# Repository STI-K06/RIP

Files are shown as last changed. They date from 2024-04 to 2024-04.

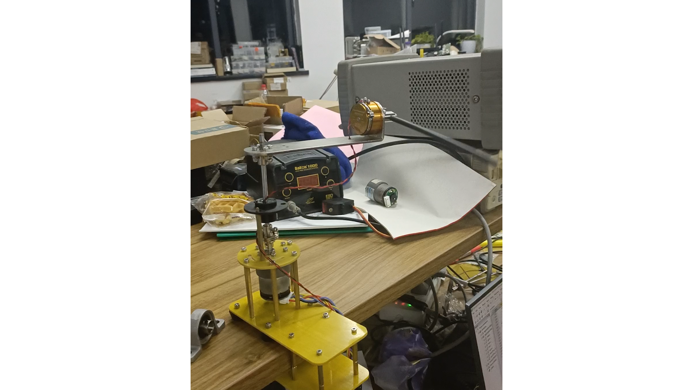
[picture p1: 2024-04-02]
hw/picture/倒立摆.png

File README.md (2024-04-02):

# 旋转倒立摆
RIP refer to *rotating inverted pendulum*  
这个分支是旋转倒立摆整体分支，分以下部分  
## doc
**存放一些文档，如题目和报告**
* 这里存放了题目和我们组当时的报告
## hw
**存放硬件与机械部分以及倒立摆实物图**  
* 硬件部分stl文件为对倒立摆所需各个部件的建模
* 根据建模并得出dxf文件用于雕刻，采用雕刻环氧板的方式搭建机械
* 此次是采用洞洞板直接焊接，因此没有设计PCB
## sw
**存放主控代码以及视觉部分python代码**  
* 主控部分采用stm32cubemx进行配置，用keil软件进行main函数编程
* 此次主控采用的是stm32f103c8t6
## 原理介绍(以后补)

## 视频链接
视频参见**https://www.bilibili.com/video/BV1mm4y1n7Gn**

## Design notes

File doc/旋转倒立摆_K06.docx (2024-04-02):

旋转倒立摆

摘要：本系统实现了一个旋转倒立摆。该系统利用STM32F103C8T6单片机作为主控制器，与电机驱动模块、减速直流电机、旋转臂、摆杆和角位移传感器一起构成摆杆角度和电机速度的双闭环调速系统。控制方式采用串级PID控制，选择减速直流电机带动旋转臂旋转，利用编码器测量电机转动的脉冲数和速度，实现速度环控制。采用角位移传感器测量摆杆的偏角，实现角度环控制。最终，系统能够较好的实现起摆、倒立、360度倒立旋转等功能，同时具有较强的抗扰动性能。

关键词：角度测量；电机控制；倒立平衡

# 1、 系统方案

## 1. 比较与选择

### 1.1 角度测量方案

方案一：三轴陀螺仪

方案二：电位器

方案比较与选择：方案一选用三轴陀螺仪检测摆杆的偏转角度，优点是可以较为精确的计算摆杆的偏转角度，缺点是传感器必须要固定在摆杆上，同时需与MCU直连以进行通信，给硬件的搭建与连接及软件的编写大大增加了难度，可行性较差。方案二选用电位器测量摆杆的偏转角度，优点是其可作为摆杆的转动主轴，可有效降低硬件部分的复杂性，并增强稳定性，且其较为简单的原理也便于软件的编写。缺点是测量时可能会因电位器的固有误差导致角度换算误差。在本设计中，摆杆的结构设计方面要求较高，不适于将传感器固定在摆杆上，且使用较高精度的电位器时同样能达到接近陀螺仪的测量效果。因此，选择方案二来实现摆杆角度的测量。

### 1.2 摆杆驱动方案

方案一：步进电机

方案二：直流减速电机

方案比较与选择：方案一采用步进电机驱动旋转臂，具有动态响应快、易于启停、易于正反转的切换及变速的优点。缺点是它以步进式跟进，角度小于一个步进角时是系统的响应盲区。方案二采用直流减速电机驱动旋转臂，优点是驱动电路简单，扭矩大，稳定性强，负载能力强。缺点是相较于直流电机转速较低。在本设计中，对电机的转速要求较小，对角度的响应精细程度和稳定性要求较大，故直流减速电机方案更为合适，因此选择方案二。

### 1.3 摆杆材料及结构选择

方案一：直径5mm长度18cm的不锈钢柱做摆杆

方案二：直径5mm长度18cm的中空碳纤维管做摆杆，尾端增加重物

方案比较与选择：方案一使用不锈钢柱作为摆杆，优点是材料易得、结构简单。缺点是转动惯量与重力力矩比值更小，由重力引起的角加速度更快，摆动更快，不利于稳定；并且整体质量更大，电机运动的阻力更大。方案二使用碳纤维管做摆杆，优点是摆杆质量可以忽略，整体转动惯量与重力力矩比值更大，由重力引起的角加速度更小，更容易控制；并且整体质量更小，电机运动的阻力更小，利于控制。缺点是材料不易得，重物的选择需要考虑。在本设计中，为使倒立摆更容易控制和达到稳态，故采用方案二。

### 1.4 固定倒立摆的底座结构选择

方案一：将倒立摆置于一个平面上，用重物压住平面

方案二：将倒立摆通过上下两面夹持的方式固定在桌子上，并用橡胶垫增大摩擦力和稳定性

方案比较与选择：方案一将倒立摆置于一个平面上，用重物压住平面，优点是结构简单，制作快。缺点是符合要求的重物质量较大，实际上不好操作。方案二将倒立摆夹持在桌子上，优点是只要桌子足够稳定，倒立摆基本上不会剧烈晃动。缺点是设计较为复杂。在本设计中，为了得到更好的稳定效果，故采用方案二。

## 2. 方案描述

系统框图如图1所示。在接收到任务执行指令后，STM32主控通过ADC通道采集角位移传感器反馈值换算成角度，并利用编码器计算得电机转动的脉冲数和转动速度。主控根据反馈值进行双环PID计算，输出PWM控制直流电机带动旋转臂运动。综上，摆杆在直流减速电机的控制之下顺利倒立，完成题目要求的相关任务。

图1 系统框图

# 2、 理论分析与计算

## 1. PID算法

如图2所示，当电位器反馈摆杆发生位移时，其变化的模拟量被MCU的AD所采集，MCU运用PID算法计算输出PWM，以控制电机的转向及转速，进而对摆杆的实时位置进行微控。

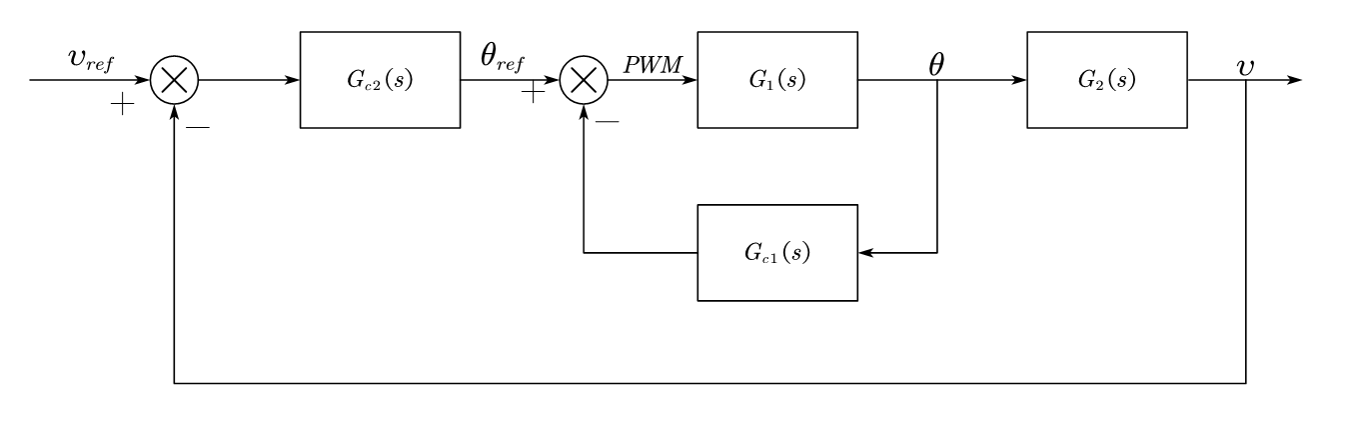
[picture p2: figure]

图 2 PID算法理论模型

## 2. 机械机构

旋转倒立摆结构如图3所示。倒立摆底座为上下两片环氧板，通过夹持方式夹在桌角。电机与底座通过6根M3铜柱相连，固定在底座上。电机转轴通过两个法兰联轴器与5mm不锈钢柱相连。不锈钢柱通过过孔导线环与转杆相连。转杆尾端放置角位移传感器。角位移传感器连接着摆杆，摆杆末端用法兰与铜柱构成重物。

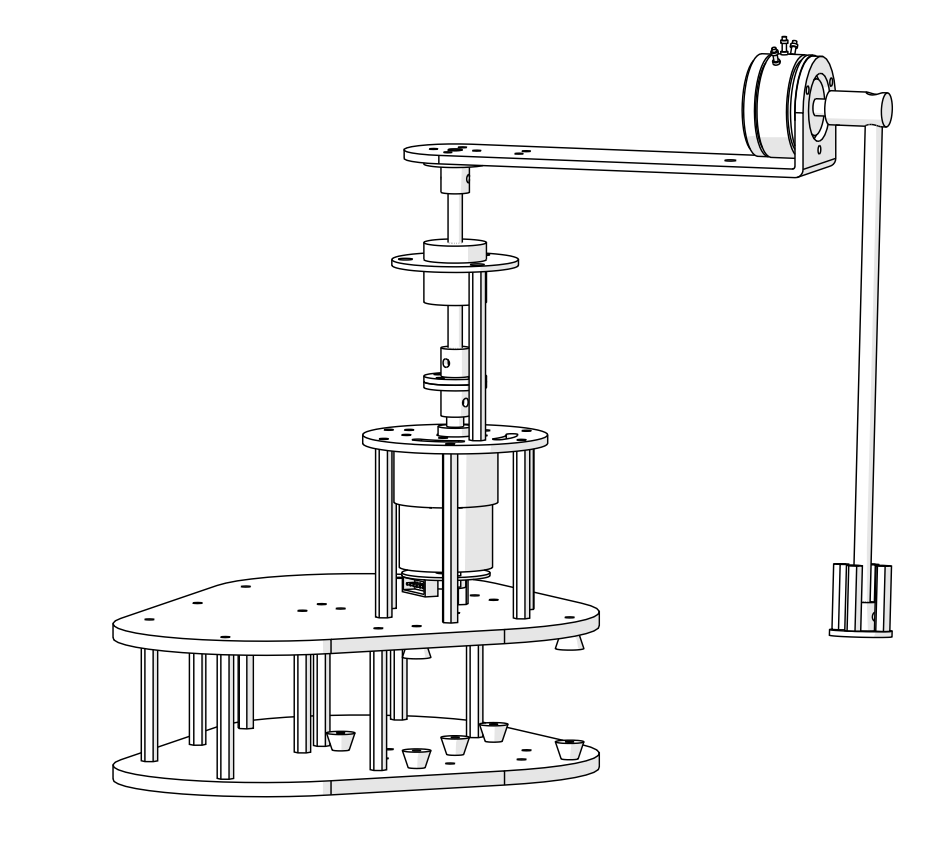
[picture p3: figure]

图3旋转倒立摆机械结构

# 3、 电路与程序设计

## 1. 电机驱动电路

如图4所示，直流电机驱动的主体为DRV8872直流电机驱动芯片，通过输入两通道PWM波的方式来控制直流电机的转速和转动方向。主控STM32可以通过输出特定1KHz频率、不同占空比的PWM波来对直流电机的转速和转动方向。

图4 电机驱动电路

## 2. 软件程序设计

程序设计流程图如图5所示。本设计中使用主控STM32控制系统，接收角度传感器数据，并利用编码器测量速度，通过PID计算输出PWM控制电机运动，完成任务要求的一系列动作。

图 5 程序设计流程图

# 4、 测试方案与测试结果

## 1. 测试环境

类型 | 品牌 | 型号
其他 | 卡西欧、SYNTEK | HS-70W型秒表、SYJDC200型角度尺

## 3. 测试方案

### 2.1摆杆起摆测试

### 摆杆从处于自然下垂状态开始，驱动电机带动旋转臂旋转使摆杆摆动，使摆角达到或超过-60°~ +60°。

### 2.2摆杆完成圆周运动测试

### 从摆杆处于自然下垂状态开始，增大摆杆的摆动幅度，直至完成圆周运动。

### 2.3摆杆由外力拉起保持倒立测试

### 外力拉起摆杆至接近 165°位置，外力撤除同时，启动控制旋转臂使摆杆保持倒立状态。

### 2.4摆杆自动起摆保持倒立测试

### 从摆杆处于自然下垂状态开始，控制旋转臂作往复旋转运动，使摆杆倒立。

### 2.5 摆杆受干扰测试

### 在摆杆保持倒立状态下，施加干扰后摆杆能继续保持倒立或 2s 内恢复倒立状态。

### 2.6 摆杆保持倒立而旋臂做圆周运动测试

### 在摆杆保持倒立状态的前提下，旋转臂作圆周运动超过一圈。

## 4. 测试结果与数据

### 3.1 摆杆起摆测试数据如表1所示

表1摆杆起摆测试

| 测试结果
序号 | 是否成功 | 起摆时间
1 | 成功 | 2.1s
2 | 成功 | 2.4s
3 | 成功 | 2.3s

### 3.2 摆杆完成圆周运动测试数据如表2所示

表2摆杆完成圆周运动测试

| 测试结果
序号 | 是否成功 | 使用时间
1 | 成功 | 3.1s
2 | 成功 | 3.5s
3 | 成功 | 3.7s

### 3.3 摆杆由外力拉起保持倒立测试数据如表3所示

表3摆杆由外力拉起保持倒立测试

| 测试结果
序号 | 是否成功 | 转动角度
1 | 成功 | 10°
2 | 成功 | 20°
3 | 成功 | 18°

3.4 摆杆自动起摆保持倒立测试数据为表4所示

表4 摆杆自动起摆保持倒立测试

| 测试结果
序号 | 是否成功 | 使用时间
1 | 成功 | 5.1s
2 | 成功 | 5.5s
3 | 成功 | 5.7s

3.5 摆杆受干扰测试数据为表5所示

表5 摆杆受干扰测试

| 测试结果
序号 | 是否成功
1 | 成功
2 | 成功
3 | 成功

3.6 摆杆保持倒立而旋臂做圆周运动测试数据为表6所示

表6 摆杆保持倒立而旋臂做圆周运动测试

| 测试结果
序号 | 是否成功 | 使用时间
1 | 成功 | 4.2s
2 | 成功 | 4.4s
3 | 成功 | 4.7s

## 5. 测试结果分析

### 4.1摆杆起摆测试

### 由测试结果知，摆杆可以迅速起摆到-60°~ +60°，满足题目要求。

### 4.2摆杆完成圆周运动测试

### 由测试结果知，摆杆可以迅速起摆直至完成圆周运动，满足题目要求。

### 4.3摆杆由外力拉起保持倒立测试

### 由测试结果知，摆杆由外力拉起后能够迅速保持倒立，满足题目要求。

### 4.4摆杆自动起摆保持倒立测试

### 由测试结果知，摆杆可以自动起摆并迅速保持倒立，满足题目要求。

### 4.5 摆杆受干扰测试

### 由测试结果知，摆杆受干扰后仍能保持倒立状态，满足题目要求。

### 4.6 摆杆保持倒立而旋臂做圆周运动测试

### 由测试结果知，摆杆在保持倒立状态的同时能够使旋臂做圆周运动，满足题目要求。

### 综上所述，本系统能够完成题目的基本要求和发挥要求。

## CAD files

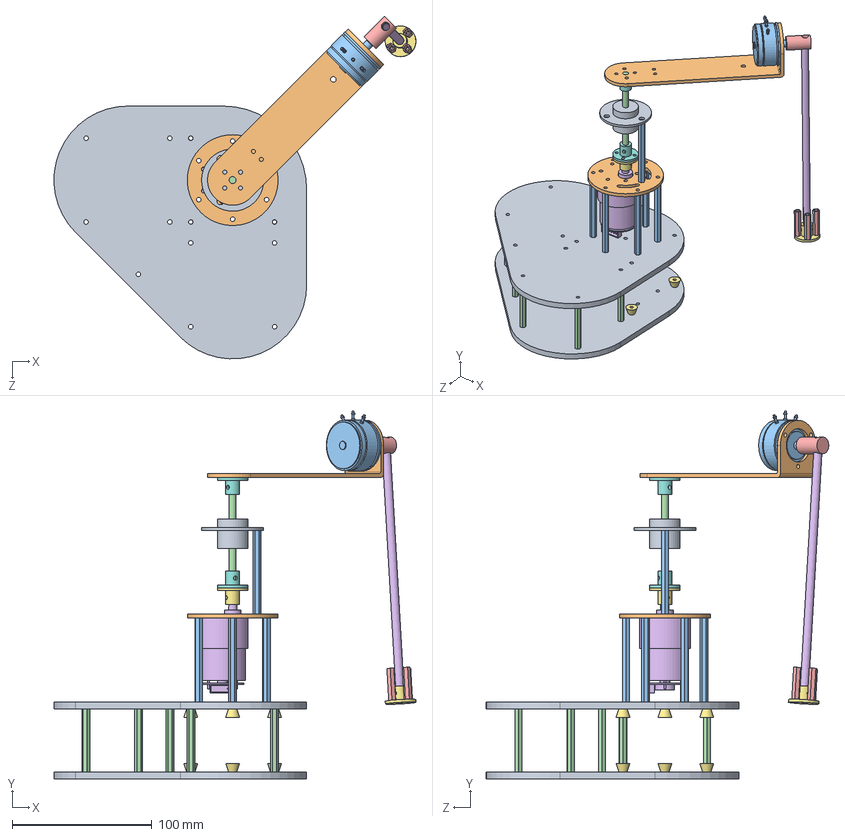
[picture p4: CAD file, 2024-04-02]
hw/stl/旋转倒立摆.SLDASM
259.3 x 263.3 x 245.4 mm
倒立摆底座 x 2
中间连接板
M3铜柱50mm x 7
M3铜柱45mm x 9
M3铜柱23mm x 4
直流减速电机带编码器
法兰联轴器 - 6mm x 2
法兰联轴器 x 2
过孔导线环
角位移传感器支架
角位移传感器
不锈钢柱子
L型联轴器
中通碳管
橡胶垫 x 10

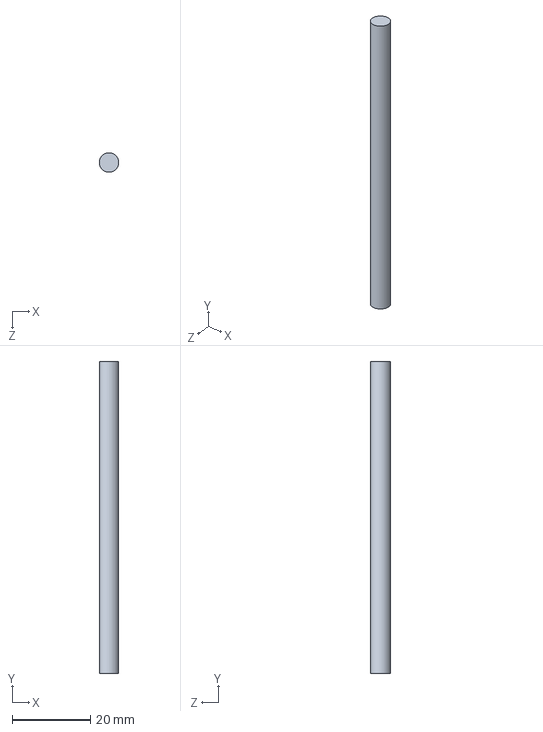
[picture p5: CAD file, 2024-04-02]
hw/stl/不锈钢柱子.SLDPRT
5.00 x 80.0 x 5.00 mm

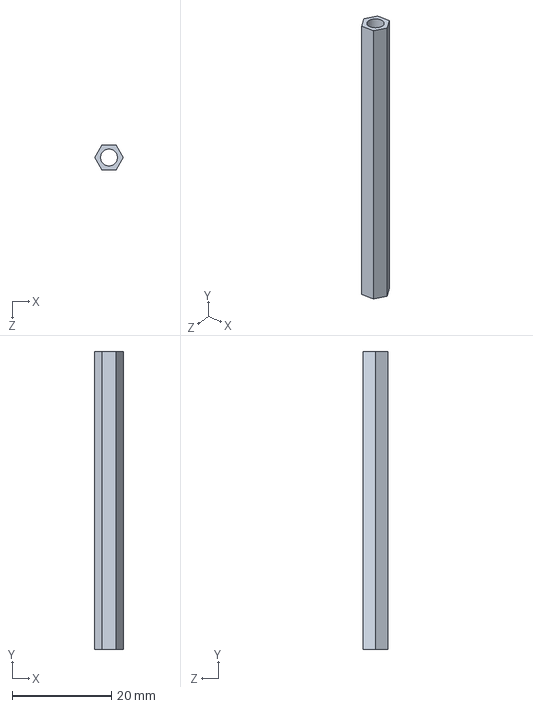
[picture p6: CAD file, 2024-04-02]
hw/stl/M3铜柱50mm.SLDPRT
5.77 x 60.0 x 5.00 mm

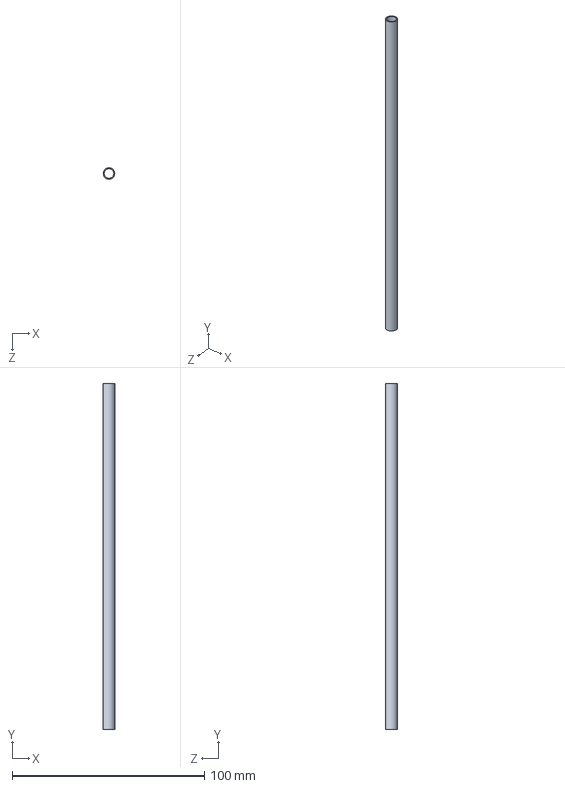
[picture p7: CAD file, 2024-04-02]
hw/stl/中通碳管.SLDPRT
6.00 x 180.0 x 6.00 mm

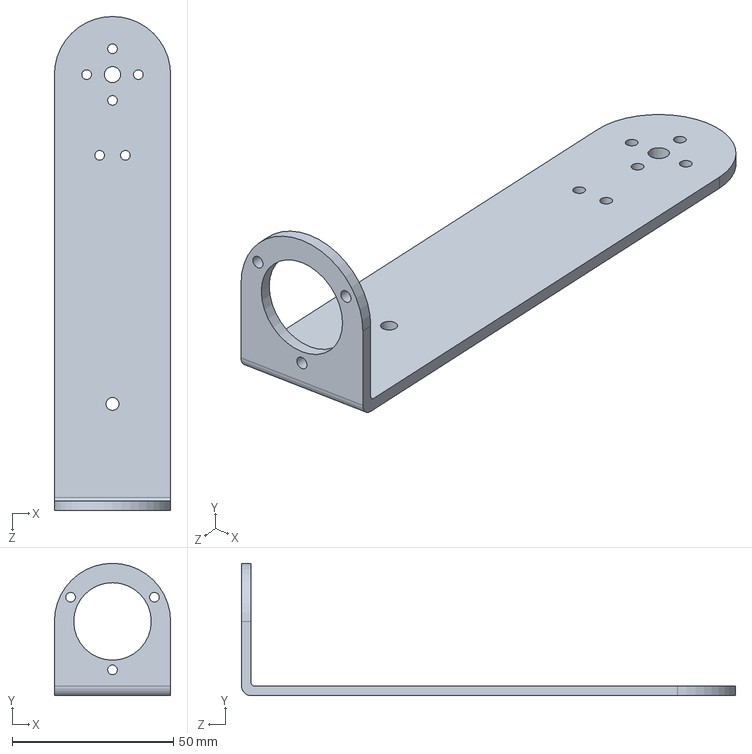
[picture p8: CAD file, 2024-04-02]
hw/stl/角位移传感器支架.SLDPRT
36.0 x 41.0 x 153.0 mm

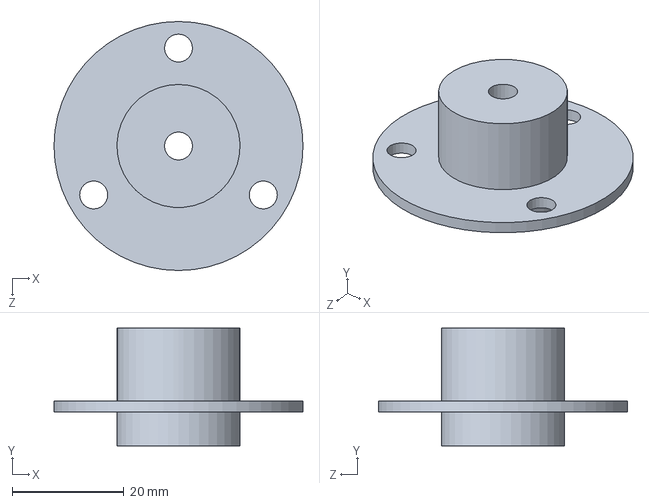
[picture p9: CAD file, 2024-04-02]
hw/stl/过孔导线环.SLDPRT
44.5 x 21.0 x 44.5 mm

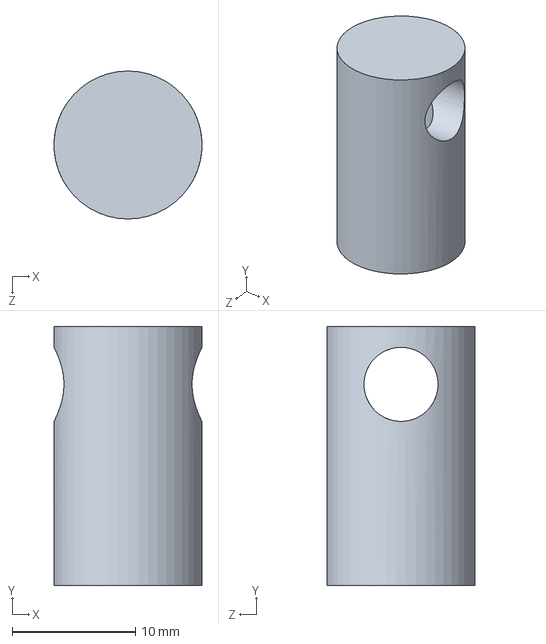
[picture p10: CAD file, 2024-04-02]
hw/stl/L型联轴器.SLDPRT
12.0 x 21.0 x 12.0 mm

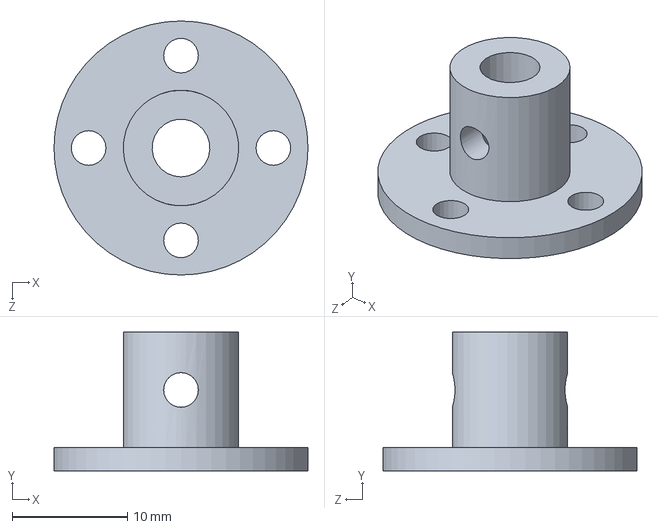
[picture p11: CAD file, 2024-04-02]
hw/stl/法兰联轴器.SLDPRT
22.0 x 12.0 x 22.0 mm

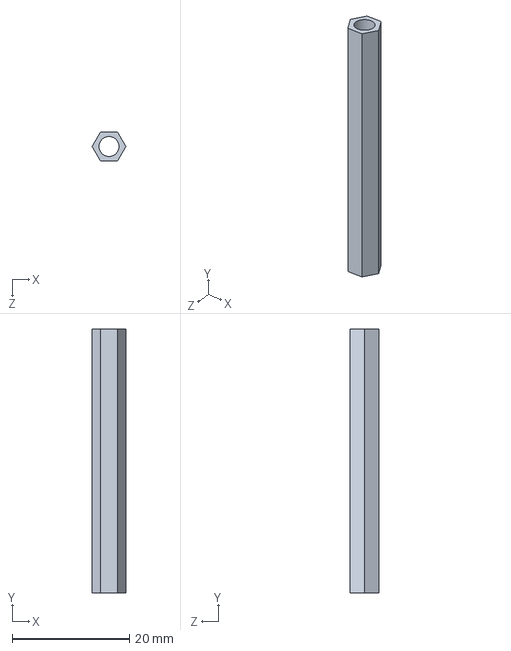
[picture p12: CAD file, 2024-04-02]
hw/stl/M3铜柱45mm.SLDPRT
5.77 x 45.0 x 5.00 mm

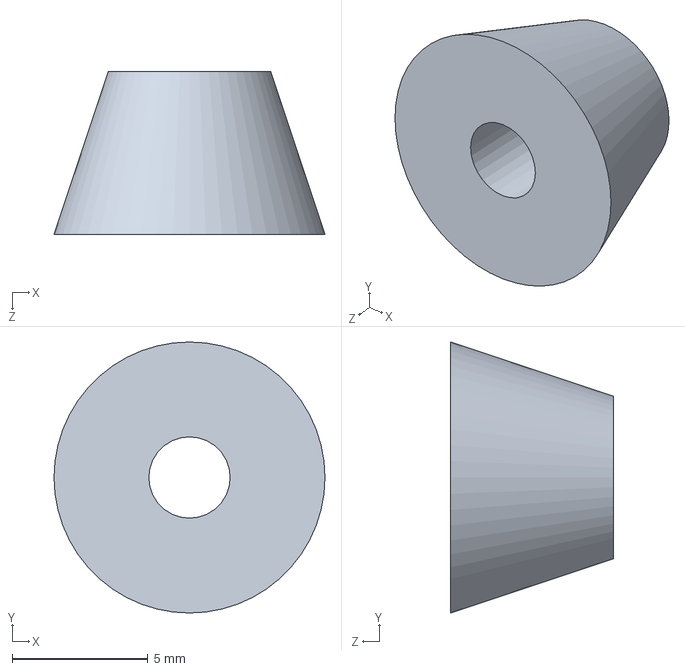
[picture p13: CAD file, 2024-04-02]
hw/stl/橡胶垫.SLDPRT
10.0 x 10.0 x 6.00 mm

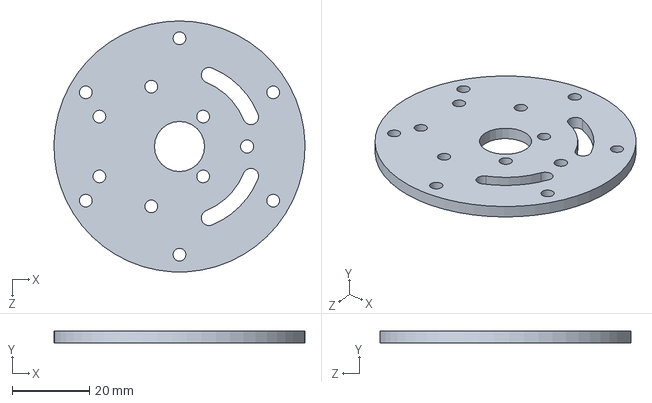
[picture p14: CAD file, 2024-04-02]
hw/stl/中间连接板.SLDPRT
65.0 x 3.00 x 65.0 mm

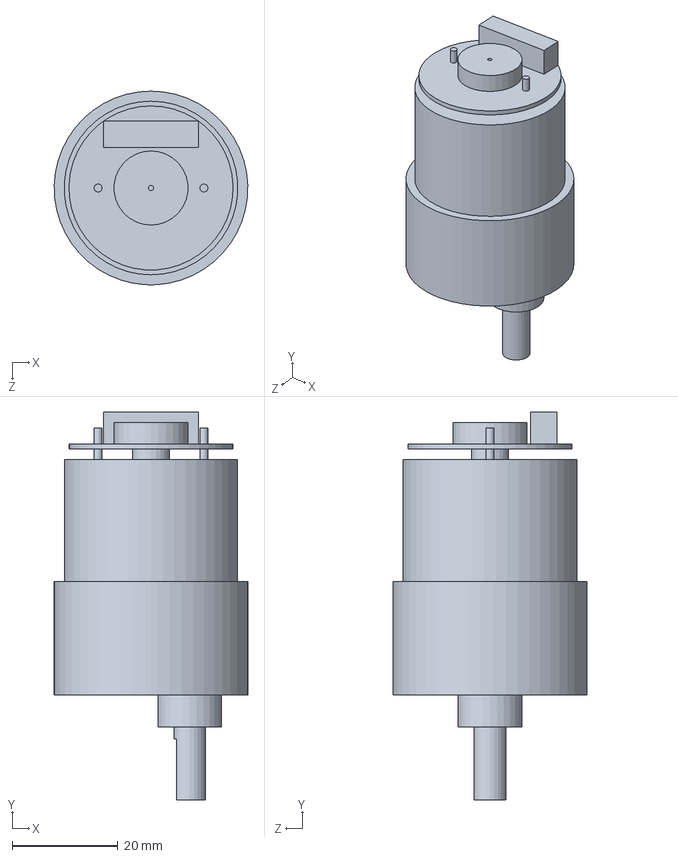
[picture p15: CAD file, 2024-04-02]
hw/stl/直流减速电机带编码器.SLDPRT
36.6 x 73.3 x 36.6 mm

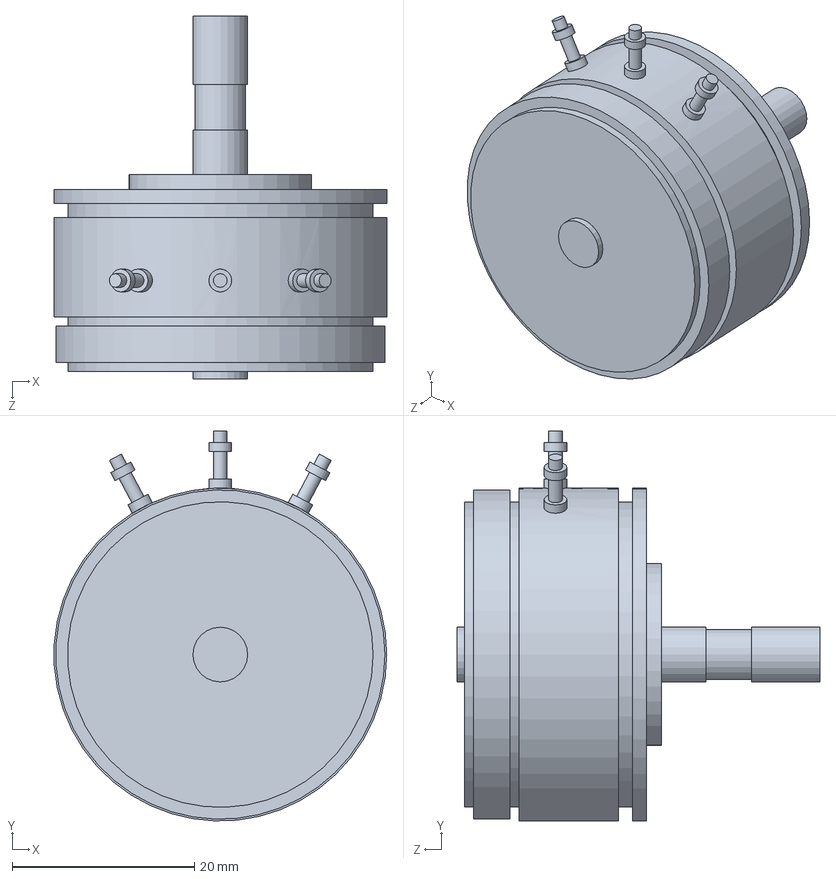
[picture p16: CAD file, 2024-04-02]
hw/stl/角位移传感器.SLDPRT
36.5 x 42.7 x 39.8 mm

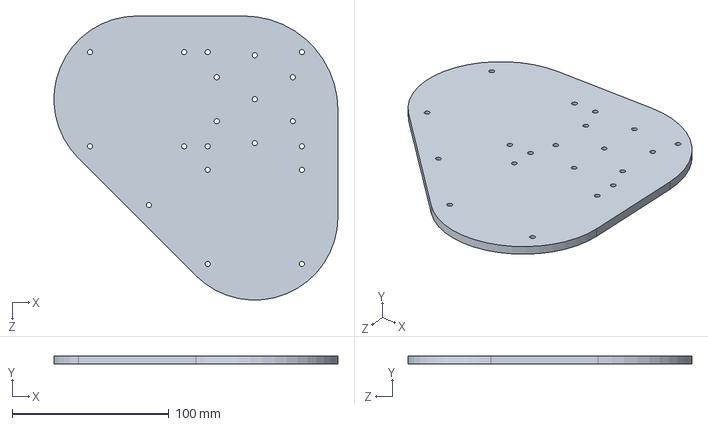
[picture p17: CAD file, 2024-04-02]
hw/stl/倒立摆底座.SLDPRT
181.0 x 5.00 x 181.0 mm

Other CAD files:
hw/stl/法兰联轴器 - 6mm.SLDPRT
hw/stl/M3铜柱23mm.SLDPRT
hw/stl/旋转倒立摆.SLDPRT

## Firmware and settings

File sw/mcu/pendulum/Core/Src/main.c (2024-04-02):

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
/* Includes ------------------------------------------------------------------*/
#include "main.h"
#include "adc.h"
#include "tim.h"
#include "usart.h"
#include "gpio.h"

/* USER CODE BEGIN Includes */
#include "math.h"
#include "stdio.h"
#include "string.h"
#include "stdlib.h"
/* USER CODE END Includes */

/* USER CODE BEGIN PTD */
struct gesture   
{
	float pulse; //脉冲数，相当于位移
	float speed; //电机旋转速度
	float voltage; //电压，模拟量
	float angle; //倒立摆角度
	float angle_last;
};
struct pidstruct  //pid参数
{
	double kp,ki,kd;
	double p,i,d;
	double thisde,lastde;
};
/* USER CODE END PTD */

/* USER CODE BEGIN PD */
uint8_t rx_buf1[1] = {0};
uint8_t rx_buf3[1] = {0};
uint16_t ADC_Value=0;
float angle_out=0;
float speed_out=0;
float position_out=0;
float angle_target=5.3;//5.3
float speed_target=0;
float position_target=0;

int mode=0;//0
int mission=0;//0

int pwm_out=0;
float cal_temp=0;
uint8_t Mission6_FLAG=1;

struct gesture gest;//当前姿态
struct pidstruct pidspeed;//速度环//逆时针为正
struct pidstruct pidangle;//角度环
struct pidstruct pidposition;//角度环
/* USER CODE END PD */


void SystemClock_Config(void);
/* USER CODE BEGIN 0 */
void DataGet1(uint8_t data)//调试
{
	
}

uint8_t reverse=0;
void DataGet3(uint8_t data)//蓝牙或串口屏
{
	
	if(data=='0')
	{
		mode=0;
		Mission6_FLAG=1;
		mission=0;
		pidspeed.p=0;
	  pidspeed.i=0;
	  pidspeed.d=0;
	  pidspeed.lastde=0;
	  pidspeed.thisde=0;
	}
	if(data=='1') mission=1;
	if(data=='2') mission=2;
	if(data=='3') mission=3;
	if(data=='4') mission=4;
	if(data=='5') mission=5;
	if(data=='6') mission=6;
	if(data=='s') mode=1;
//	if(data=='4') mode=4;
//	if(data=='r') reverse=!reverse;
	
}
void Wheel(int pwm)//轮子调速
{
	int direct;
	
	if(pwm>1000)
		pwm=1000;
	if(pwm<-1000)
		pwm=-1000;
	if(pwm>0)
		direct=1;
	if(pwm<0)
		direct=0;
	switch(direct){
	case 1:
		__HAL_TIM_SET_COMPARE(&htim2,TIM_CHANNEL_1,1000-pwm);
	  __HAL_TIM_SET_COMPARE(&htim3,TIM_CHANNEL_2,1000);
		break;
	case 0 :
		__HAL_TIM_SET_COMPARE(&htim2,TIM_CHANNEL_1,1000);
		__HAL_TIM_SET_COMPARE(&htim3,TIM_CHANNEL_2,1000+pwm);
		break;
	}	
}
struct pidstruct initPID(float kp,float ki,float kd)//pid初始化
{
	struct pidstruct e;
	e.kp=kp;
	e.ki=ki;
	e.kd=kd;
	e.p=0;
	e.i=0;
	e.d=0;
	e.lastde=0;
	e.thisde=0;
	return e;
}
float PID(struct pidstruct *e,float err,float outlow,float outhigh,float a,float int_k)//计算输出
{
	float out;
	e->thisde = err*(1-a) + e->lastde*a;
	e->p = e->kp * e->thisde;
	e->i = e->i + e->ki * e->thisde;
	e->i *= int_k;
	e->d = e->kd * (e->thisde - e->lastde);
	e->lastde = e->thisde;
	out = e->p + e->i + e->d;
	if(e->i > outhigh) e->i=outhigh;
	if(e->i < outlow) e->i=outlow;
	if(out>outhigh) out=outhigh;
	if(out<outlow) out=outlow;
	return out;
}
void Read_Encoder(void)//读取计数器的值
{
		static int catch1[3];
    catch1[1]=__HAL_TIM_GET_COUNTER(&htim1);
    catch1[2]=catch1[1]-catch1[0];
	  catch1[0]=catch1[1];
    gest.pulse=0.025f*(32768-catch1[1]);
    gest.speed=-catch1[2]*0.025f;
}
void ADC_Cal()
{
	gest.angle_last = gest.angle;
	gest.voltage=ADC_Value;
	gest.angle=(ADC_Value-1470)*0.087912f-180;//左正右负
	if(gest.angle<-180)
		gest.angle=gest.angle+360;
}

void HAL_UART_RxCpltCallback(UART_HandleTypeDef *huart)  //串口中断
{
	if(huart == &huart1)
	{
		DataGet1(rx_buf1[0]);
		HAL_UART_AbortReceive_IT(&huart1);
		HAL_UART_Receive_IT(&huart1, rx_buf1, 1);
	}
	if(huart == &huart3)
	{
		DataGet3(rx_buf3[0]);
		HAL_UART_AbortReceive_IT(&huart3);
		HAL_UART_Receive_IT(&huart3, rx_buf3, 1);
	}
}

float int_k=1;
void HAL_TIM_PeriodElapsedCallback(TIM_HandleTypeDef *htim)//定时器中段
{
	static int k=0,k1=0,delay_count=0,delay_flag=1,current_x=0;
	k1++;
	if(k1>=10)
	  Read_Encoder(),k1=0;	
//	if(k1>=50&&(cal_temp>0.5||cal_temp<-0.5))
//		k1=0,pidspeed.i/=1.5;		//1.58
//	else if(k1>=50&&(cal_temp>0.3||cal_temp<-0.3))
//		k1=0,pidspeed.i/=1.3;		//1.2
//	else if(k1>=50&&cal_temp<0.2&&cal_temp>-0.2)
//		k1=0,pidspeed.i/=1.1;
//	else if(k1>=50&&cal_temp<0.1&&cal_temp>-0.1)
//		k1=0;
	
	if(mode==0)//停止运动
	{
		k=0;
		__HAL_TIM_SET_COMPARE(&htim2,TIM_CHANNEL_1,1000);
		__HAL_TIM_SET_COMPARE(&htim3,TIM_CHANNEL_2,1000); 
	}
	else if(mode==1)//倒立
	{
		if(gest.angle<(angle_target+30) && gest.angle>(angle_target-30))
		{
			k++;
			if(k==10)
			{
				//Read_Encoder();
				speed_out =PID(&pidspeed,speed_target-gest.speed,-15,15,0.7,int_k);	//0.94
				k=0;
			}
			angle_out = PID(&pidangle,angle_target-speed_out-gest.angle,-900,900,0,1);
			Wheel(angle_out);
		}
		else
		{
			k=0;
			__HAL_TIM_SET_COMPARE(&htim2,TIM_CHANNEL_1,1000);
			__HAL_TIM_SET_COMPARE(&htim3,TIM_CHANNEL_2,1000); 
		}	
	}
	else if(mode==2)//起摆
	{
		if(gest.angle>165 && gest.angle<180 && gest.angle_last>165 && gest.angle_last<180)
		{
			if(gest.angle>gest.angle_last)
				Wheel(-200);
			else if(gest.angle<gest.angle_last)
				Wheel(200);
		}
		else if(gest.angle<-165 && gest.angle>-180 && gest.angle_last<-165 && gest.angle_last>-180)
		{
			if(gest.angle>gest.angle_last)
				Wheel(-200);
			else if(gest.angle<gest.angle_last)
				Wheel(200);
		}
	}
	else if(mode==3)//起摆
	{
		if(gest.angle>165 && gest.angle<180 && gest.angle_last>165 && gest.angle_last<180)
		{
			if(gest.angle>gest.angle_last)
				Wheel(-140);
			else if(gest.angle<gest.angle_last)
				Wheel(140);
		}
		else if(gest.angle<-165 && gest.angle>-180 && gest.angle_last<-165 && gest.angle_last>-180)
		{
			if(gest.angle>gest.angle_last)
				Wheel(-140);
			else if(gest.angle<gest.angle_last)
				Wheel(140);
		}
	}
	if(mission==0)
	{
		delay_count=0,delay_flag=1;
	}
  else if(mission==1)
	{
		if(delay_flag==1)
		{
			Wheel(150);
			delay_count++;
			if(delay_count==500)
				delay_count=0,delay_flag=0,mode=2;
		}
		if(gest.angle>-90 && gest.angle<90)
			mode=0,mission=0;
	}
	else if(mission==2)
	{
		if(delay_flag==1)
		{
			Wheel(150);
			delay_count++;
			if(delay_count==500)
				delay_count=0,delay_flag=0,mode=2;
		}
		if(gest.angle>-10 && gest.angle<10)
			mode=0,mission=0;
	}
	else if(mission==3)
	{
		mode=1;
		mission=0;
	}
	else if(mission==4)
	{
		if(delay_flag==1)
		{
			Wheel(150);
			delay_count++;
			if(delay_count==300)
				delay_count=0,delay_flag=0,mode=3;
		}
		if(gest.angle<(angle_target+15) && gest.angle>(angle_target-15))//20
			mode=1;
		if(gest.angle>(angle_target+90) || gest.angle<(angle_target-90))
			mode=3;
	}
	else if(mission==5)
	{
		if(gest.angle<(angle_target+15) && gest.angle>(angle_target-15))
			mode=1;
		if(gest.angle>(angle_target+90) || gest.angle<(angle_target-90))
			mode=3;
	}
	else if(mission==6)
	{
		if(Mission6_FLAG)
		{
			mode=1,speed_target=0.2;
			current_x=gest.pulse+39,Mission6_FLAG=0;
		}
		if(gest.pulse>=current_x)
		{
			speed_target=0;	
			mission=0,Mission6_FLAG=1;
		}
		
	}
}
	
//	if(mode==0)
//	{
//		__HAL_TIM_SET_COMPARE(&htim2,TIM_CHANNEL_1,1000);
//		__HAL_TIM_SET_COMPARE(&htim3,TIM_CHANNEL_2,1000); 
//		return;
//	}
//	else if(mode==1)
//		pwm_out=100;
//	else if(mode==2)
//		pwm_out=200;
//	else if(mode==3)
//		pwm_out=300;
//	else if(mode==4)
//		pwm_out=400;
//	if(reverse) 
//		pwm_out=-pwm_out;
//	Wheel(pwm_out);
/* USER CODE END 0 */

/**
  * @brief  The application entry point.
  * @retval int
  */
int main(void)
{
  /* MCU Configuration--------------------------------------------------------*/

  /* Reset of all peripherals, Initializes the Flash interface and the Systick. */
  HAL_Init();

  /* Configure the system clock */
  SystemClock_Config();

  /* Initialize all configured peripherals */
  MX_GPIO_Init();
  MX_TIM1_Init();
  MX_TIM2_Init();
  MX_TIM4_Init();
  MX_USART1_UART_Init();
  MX_USART3_UART_Init();
  MX_ADC1_Init();
  MX_TIM3_Init();
  /* USER CODE BEGIN 2 */
	HAL_ADCEx_Calibration_Start(&hadc1);    //AD校准
	
	HAL_UART_Receive_IT(&huart1,rx_buf1,1);
	HAL_UART_Receive_IT(&huart3,rx_buf3,1);
	HAL_TIM_PWM_Start(&htim2,TIM_CHANNEL_1);
	HAL_TIM_PWM_Start(&htim3,TIM_CHANNEL_2);
	HAL_TIM_Base_Start_IT(&htim4);
	HAL_TIM_Encoder_Start(&htim1,TIM_CHANNEL_ALL);
	
//	pidspeed=initPID(6.2,0.5,3.4);	//0.008   0.0035		//6 0.5 3.2(is able to keep for 20min)
	int_k=0.95;
	pidspeed=initPID(0,3.2,0);			//1.2
	//pidspeed=initPID(0,0,0);
	pidangle=initPID(115*0.7*0.7,0,2200*0.7*0.7);			//115*0.6=69	2200*0.6=1320
	__HAL_TIM_SET_COUNTER(&htim1,32768);
  /* USER CODE END 2 */

  /* Infinite loop */
  /* USER CODE BEGIN WHILE */
  while (1)
  {
    /* USER CODE END WHILE */

    /* USER CODE BEGIN 3 */
		 //Wheel(200);
		 HAL_ADC_Start(&hadc1);     //启动ADC转换
     HAL_ADC_PollForConversion(&hadc1, 50);   //等待转换完成，50为最大等待时间，单位为ms
     if(HAL_IS_BIT_SET(HAL_ADC_GetState(&hadc1), HAL_ADC_STATE_REG_EOC))
		 {
			 ADC_Value = HAL_ADC_GetValue(&hadc1);   //获取AD值
			 ADC_Cal();
		 }
//		 if(gest.speed<0.1&& gest.angle>-0.1)
//			pidspeed.i=0;
		 printf("%.2f",speed_target);
		 //printf("1");
     //HAL_Delay(200);
  }
  /* USER CODE END 3 */
}

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
/* USER CODE BEGIN 4 */
int fputc(int ch, FILE *f)
{
	HAL_UART_Transmit(&huart1 ,(uint8_t*)&ch,1,10);
	return ch;
}
/* USER CODE END 4 */
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


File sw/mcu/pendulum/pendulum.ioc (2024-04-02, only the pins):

Mcu.UserName=STM32F103C8Tx
PA0-WKUP.Signal=S_TIM2_CH1_ETR
PA1.Signal=ADCx_IN1
PA13.Signal=SYS_JTMS-SWDIO
PA14.Signal=SYS_JTCK-SWCLK
PA8.Signal=S_TIM1_CH1
PA9.Signal=S_TIM1_CH2
PB10.Signal=USART3_TX
PB11.Signal=USART3_RX
PB12.Signal=GPIO_Input
PB5.Signal=S_TIM3_CH2
PB6.Signal=USART1_TX
PB7.Signal=USART1_RX
PD0-OSC_IN.Signal=RCC_OSC_IN
PD1-OSC_OUT.Signal=RCC_OSC_OUT

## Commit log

2024-04-02 增加旋转倒立摆stl部分
    [L型联轴器.SLDPRT, M3铜柱23mm.SLDPRT, M3铜柱45mm.SLDPRT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]
2024-04-02 除了图片均已上传

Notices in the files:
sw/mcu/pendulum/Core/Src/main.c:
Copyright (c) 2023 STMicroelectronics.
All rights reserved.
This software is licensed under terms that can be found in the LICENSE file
